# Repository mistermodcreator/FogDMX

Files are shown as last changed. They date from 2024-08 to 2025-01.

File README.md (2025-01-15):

# FogDMX
First, I'm not a programmer. My code will be janky and unoptimised, but it should work.

Well, hello. Since you are here, you are probably looking for a cheap and easy way to upgrade your generic fog machine to use DMX and to have an variable output. So was I. As I found out, there is no affordable product out there to do that. So I decided to try programming Arduino and a few weeks later, the project was finished.

## Version 2.0 coming soon
Notable features include support for a pwm-controlled fan (it will always use two dmx-channels) and the `nd` when no DMX-signal is detected will flash now.

## What can this do?
This project is essentially two things: An DMX interface to controll a fog machine via DMX, OR a manual remote with an variable output. 
A fixture profile for Daslight is available (Manufacturer: `_Generic`  profile name: `FogDMX 2.0`)

## Tested hardware & Disclaimer
The project is tested on an `ADJ VF 1300`, but as long as your fog machine is triggered using low voltage signals to a control board inside the machine, everything should be fine. If it doesn't and the wires in the remote are as thick as normal power cables, STOP IMMEDIATELY! This probably means that your fogger uses high voltage to trigger, which means that you will take a lot more risk when doing this.
I am not responsible for any damage that might happen when you do this. Just think yourself and stop if you are not comfortable with what you are doing at any point.

## What's included here?
Included are the code, a list of materials and 3D-Models for an enclosure fitting my switches and my potentiometer. You can modify the [3D model](https://www.tinkercad.com/things/fHhk7ptpsdN-fogdmx-case) to match your components.

## Materials (non-affiliate links):
- [Arduino Uno or semilar (I used a Nano)](https://www.amazon.de/dp/B0097AU5OU?psc=1)
- The Arduino-IDE on your computer
- [A MAX-485-board](https://www.amazon.de/dp/B0785B3BS8?psc=1)
- [A Relay](https://www.amazon.de/dp/B07FNGCSZQ)
- [A TM1637 based 4 digit 7-segment-display](https://www.amazon.de/dp/B078S8SGW2)
- [Two switches and one push button](https://www.amazon.de/dp/B099YM8WC3)
- 1 potentiometer
- [1 Female](https://www.thomann.de/de/amphenol_ac3fdz.htm) and [1 Male](https://www.thomann.de/de/amphenol_ac3mmdz.htm) XLR socket
- [1 Female MIDI-socket](https://www.thomann.de/de/rean_nys_325.htm) (Connection to fog machine, if your machine uses another type of connector or a hard wired remote, pick up a matching socket or route the wires directly in the enclosure)
- 3D printer (If you don't have one, you can use a lunch box or semilar) [3D model](https://www.tinkercad.com/things/fHhk7ptpsdN-fogdmx-case)
- Some wires
- Heatshrink
- Hot Glue
- 5V power supply (if your fog machine doesn't output 5V on its own, machines with wireless remotes often do that)

## So, how to build this?
- First, download the arduino sketch and open it in Arduino IDE. Then, use the library manager to install `TM1637 Driver (by AKJ, Version 2.1.2)` and `DMXSerial (by Matthias Hertel, Version 1.5.3)`
- Now take a look at the values on top. If you want, you can modify these to fit your needs. What these values do is explained next to them and under **tuning**. **WARNING!** If you modify these values, your fog machine might not respond or the following instructions might not name the right connections to make anymore. If you are unsure about this, try the default values first.
- Now plug in your Arduino and upload the sketch. This way, you will be able to test as you solder up or plug in the connections.

### The time has come to connect up your components.
You can use dupont-connectors, however for reliability-reasons I wouldn't reccoment them in the final assembly. Soldering is not that hard and it WILL be a nightmare to diagnose one loose connection (naturally right when the machine needs to work)

- I would reccomend starting with the signal wires, as positive and ground connections need to be grouped together later.
- First solder your wires to the individual componets and make connections to the arduino last, ideally after figuring out the placement of all components in your case.

#### But what goes where?
- Display: 	`CLK -> Pin 3`		`DIO -> Pin 4`		`GND -> GND`		`VCC -> +5V`
- Relais: 	`IN -> Pin 5`		`GND -> GND`		`VCC -> +5V`
- MAX-485:	`GND -> GND + DE`		  `VCC -> +5V`		`B -> DMX-Pin 2	A -> DMX-Pin 3`	  	`R0 -> D0/RX (Through a switch)`
- Push-Button:	Connect between Pin 6 and GND
- Switch:				Connect between Pin 7 and GND
- Pot:					Connect between A0 and GND, ensuring the far left position gives the least resistance
- DMX-Out: 			Can just be connected to the corresponding pins on DMX-In
- MIDI-In:			Bit complicated. Grap a multimeter and figure out, where ground, +5V and the trigger pin are, when connected to your fog machine. Then connect GND to GND, +5V to +5V and the trigger through the normally open contacts of the relay to GND. If you do this the wrong way around (through normally closed), don't panic as this is fixable in software (will just take a few minutes)

### Now, TEST!
Connect you new controller to your fog machine and DMX-controller and test everything. If all went right, you should now have a fully functioning DMX-controlled fog machine!
**Don't forget to glue down everything in the enclosure with hot glue (and maybe cable-manage better than me)**

# How to use the controller
Start it by connecting to power, either through the fog machine or, if you want to test without fog, by using a USB power bank. The controller will start and greet you with `HI`, then it will display the current mode. This is a good time to rotate the external switch to match up with the legend on the box. If you missed the mode, no problem! Just switch modes, the newly selected mode will be displayed.
### d512 - DMX-mode
Your controller now listens for a DMX-signal and displays the channel it is listening on. To change the channel, press the push-button and rotate the pot. The channel shown in the display will be set once you let go of the push-button. In order to start on a specific channel every time, check out **Tuning**.

### bUtn - Manual mode
Your controller displays the current pot value in the display (range same as DMX-channel, `0-255`). When you press the push-button, your fog machine will fire as if that DMX-value was set via DMX. You CAN rotate the pot while firing, just mind that because of my poor programming skills, the rate at which the pot is polled (asked for its value) is proportional to its value. The lower the value, the longer it will take for a change to be registerd while firing.

# Tuning
Since the sketch allows for customization, I will mention the tuning that might be done. Nothing here can break your stuff, however it can absolutely result in the remote not functioning. Just reupload the original sketch and you should be fine! Speaking of, any time you change a value, you will need to reupload the sketch to your arduino. Since the serial connection (and the Nano has only one) is used by the DMX-Input, you can't simply upload, as the same interface is used for USB-communication. This is where that switch in `R0 -> D0/RX` comes into play. Flipping it off shuts off the DMX-connection, allowing you to upload your sketch. Just remember to flip it back on afterwards, else you can't get a DMX-signal, no matter how hard you try.

#### Timings
On top of the sketch, you can adjust a few timings: How long the signal (to the fog machine) is on and the minimum and maximum time the signal is switched off, essentially allowing you to adjust the range available.
In terms of timing (how long the signal is on), lower = better. Turn this number down and test if your fog machine still responds every time you hear the relais. Keep going until it doesn't anymore and then back off slightly, to get a reliable setting. **NOTE:** With a mechanical relay, there is a limit to how fast you can go. For my relay, it was ~7ms. 
If your fog machine doesn't respond every time on default settings, increase the number until it responds every time and then add a few ms to be safe.
The range adjustment should need no explanation. `min` is the offtime for minimal output and `max` the offtime for maximal output of fog.

#### DMX-related settings
On top there are also two DMX-related settings: The default channel and the minimal DMX-value required to turn the output on. There isn't much more to it.

#### Pot-range
In lines `110 to 112` and `125 to 127` you can see how the pot input (which can be between 0 and 1023) is mapped to the required range of values.
```
        if(pot_val >= 15 && pot_val <= 700){pot_val=map(pot_val, 15, 700,1,64);}
        else if(pot_val < 15){pot_val = 1;}
        else if(pot_val > 700){pot_val = 64;}
```
**This is to map the pot for DMX-channel selection**, where `15` is the minimal value and `700` the maximal value. You can also change the range of channels available for manual selection, where `1` is minimum and `64` is maximum. Depending on your pot, you might change these values to allow for full use of the rotation of your pot or to make channel selection easier or make more channels available.

#### Inverting relay
Whereever the software writes to the relay, `digitalWrite(out,X)` is used. X is the value written. Just swap 1's with 0's and the other way around.

## Known bugs - Fixes much appreciated :-)
- DMX-signal detection doesn't work right. When a DMX-signal is present, all is fine. When it is lost, the controller switches between having a DMX-signal and not having one periodically, even when nothing is connected to the DMX-ports.
- Program essentially stops when waiting, which can delay responses by up to 1s (default values). Async waits would be a solution, however I can't program that.

## Features I'm too dumb to program - pls send help
- Support for a pixel-based display. I've looked into it, but couldn't find a library that would allow me to print simple text as that's all thats needed (right now)
- Timer function
- Support for a PWM-out to control a fan through a second DMX-channel. The fan should turn off when no fog is triggered and turn on at the set value when the DMX-command for fog is recieved, however before the actual fog is triggered (to allow it to spin up, the delay should be configurable).

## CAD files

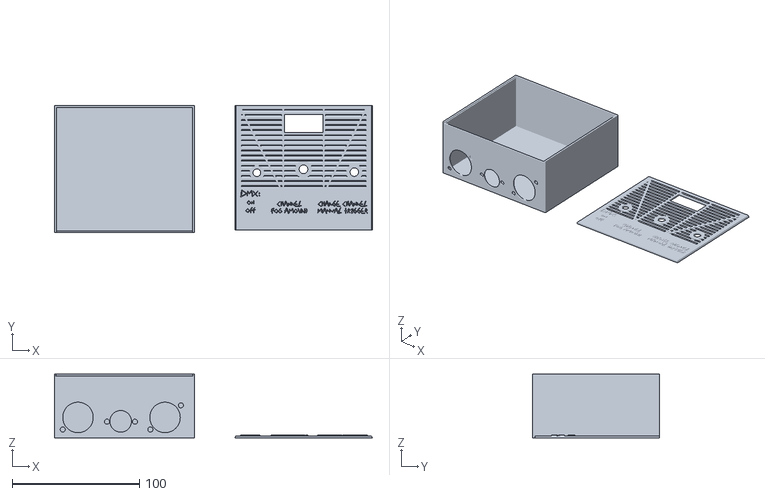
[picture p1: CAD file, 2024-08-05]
Case.stl
250.3 x 100.3 x 50.0

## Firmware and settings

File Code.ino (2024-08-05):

// TM1637 Driver - Version: 2.1.2
#include <TM1637.h>

#include <DMXSerial.h>

const int status_led = 13;      //The pin to use for the status led (13 being the internal LED)
const int out = 5;              //The pin to use for relais/mosfet control

const int dmx_switch = 7;       //The pin to use to read the switch to disabel/enable manual control
const int pot_pin = A0;         //The pin to use for the pot input when manually controling
const int manual_pin = 6;       //The pin to use for the manual fog trigger

int channel = 1;                //The default DMX Adress to listen to
const int min_val = 2;         //Min DMX value to turn output on

const int ontime = 20;          //How long to turn Output on
const int min = 1000;            //Offtime for min Output
const int max = 0;             //Offtime for max Output

const int dmx_act_min = 1000;    //Max time between DMX Packets before an error is displayed

//Display pin config (CLK, DIO)
TM1637 tm(3, 4);

//Initialize all used variables as save values
int nodmx = 0;
int dmx_act = 0;
int in = 0;
int pot_val = 0;
int manual_trigger = 0;
int dmx_switch_state = 2;
int pot_perc = 0;
int waitnum = 999;
int old_dmx_switch_state = 10;

void setup() {
//Init DMXSerial as Reciever and set pinmodes
  DMXSerial.init(DMXReceiver);
  pinMode(status_led, OUTPUT);
  pinMode(out, OUTPUT);
  pinMode(dmx_switch, INPUT_PULLUP);
  pinMode(pot_pin, INPUT_PULLUP);
  pinMode(manual_pin, INPUT_PULLUP);
  digitalWrite(out, 1);
  //startup display driver
  tm.begin();
  tm.setBrightness(2);
  tm.clearScreen();
  tm.display("HI");
  delay(1500);
  tm.clearScreen();
}

void loop() {
  delay(30);
  tm.display("    ");
  old_dmx_switch_state = dmx_switch_state;
  dmx_switch_state=digitalRead(dmx_switch);
  if(dmx_switch_state != old_dmx_switch_state) {
    if(dmx_switch_state == 1){
      tm.display("D512");
      delay(1000);
      tm.clearScreen();}
    if(dmx_switch_state == 0){
      tm.display("BUTN");
      delay(1000);
      tm.clearScreen();}
  }
  //Check for DMX Activity, turn off status light and write to var if no activity
  dmx_act = DMXSerial.noDataSince();

  if(dmx_act > dmx_act_min && dmx_switch_state == 1){
    digitalWrite(status_led, 0);
    nodmx = 1;
    tm.display("nDMX");
  }
  if(dmx_act < dmx_act_min){
    digitalWrite(status_led, 1);
    nodmx = 0;
  }
  
  if(dmx_switch_state==1){
    // Turn output off (for safety, should already be off)
    digitalWrite(out, 1);

    if(nodmx == 0){
      in = DMXSerial.read(channel);
      manual_trigger=digitalRead(manual_pin);   //Read manual trigger
      tm.display(channel);
    
      if(in < 255){     //Check if not 100%
      
        // Turn output off (for safety, should already be off)
        digitalWrite(out, 1);
        if(in > min_val){   //Check if DMX Value is above min
          waitnum = map(in, 0, 255, min, max);
          digitalWrite(out, 0); //Turn output on, then wait for calculated time
          delay(ontime);
          digitalWrite(out, 1);
          delay(waitnum);
        }
      
      }
      if(in == 255){
        digitalWrite(out,0);    //Turn Output on when DMX Value is 255
      }

      if(manual_trigger==0){
        pot_val=analogRead(pot_pin);            //Read pot
        if(pot_val >= 15 && pot_val <= 700){pot_val=map(pot_val, 15, 700,1,64);}
        else if(pot_val < 15){pot_val = 1;}
        else if(pot_val > 700){pot_val = 64;}
        channel=pot_val;                        //Set Channel as pot value
      }
    }
  
    else{
      digitalWrite(out, 1);   //Wenn kein DMX, Output aus
    }
  
  }
  if(dmx_switch_state==0){      //When dmx is turned off, read pot and map to 0-255
    
    pot_val = analogRead(pot_pin);
    if(pot_val <= 700 && pot_val >= 5) {pot_val = map(pot_val,5,700,0,255);}
    if(pot_val > 700){pot_val = 255;}
    if(pot_val < 2){pot_val = 0;}
    manual_trigger = digitalRead(manual_pin);   //Read manual trigger
    tm.display(pot_val);                       //Display pot value
    
    if(manual_trigger == 0){                      //When fog triggered
      if(pot_val < 255 && pot_val >= min_val){    //Check if pot is not 100% and above min
        waitnum = map(pot_val, 0, 255, min, max); //Map pot to min and max value
        digitalWrite(out, 0);                     //Turn output on for time set on top
        delay(ontime);
        digitalWrite(out, 1);                     //Wait for time maped from pot value
        delay(waitnum);
      }
      
      if(pot_val == 255){
        digitalWrite(out,0);    //When pot is 100%, just press the button
      }
    }
    else{
      digitalWrite(out, 1);
    }
  }
}
